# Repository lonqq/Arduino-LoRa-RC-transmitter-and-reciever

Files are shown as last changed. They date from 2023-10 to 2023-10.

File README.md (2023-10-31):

# Arduino based RC system
The ultimate DIY radio control system.
Remotely operate model airplanes, multicopters, boats, land vehicles, robots, or anything you can imagine.
<p align="left">
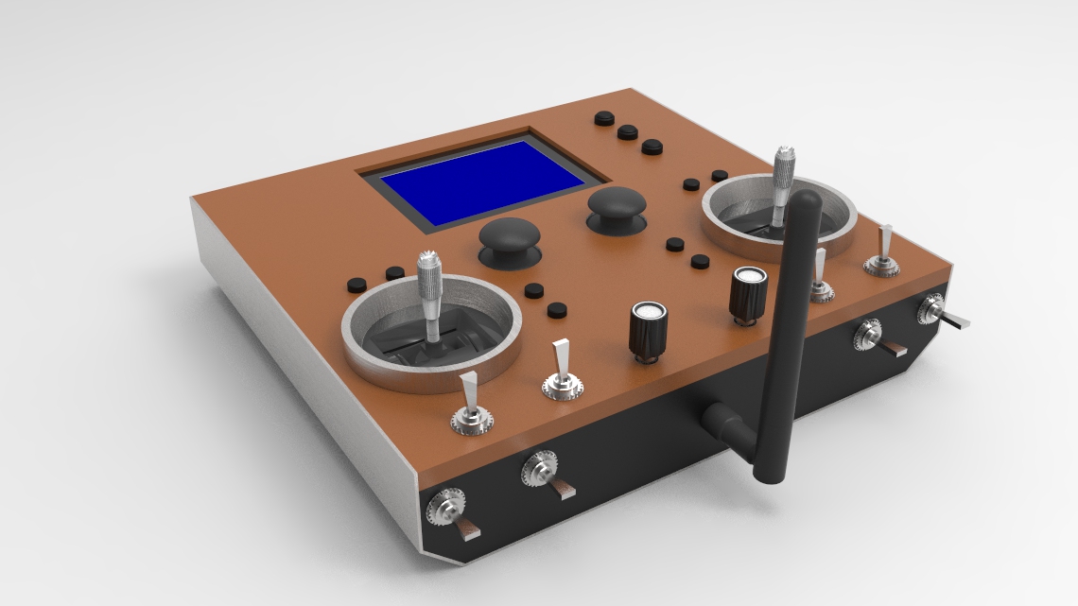
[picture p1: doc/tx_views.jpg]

</p>

## Main features
- 20 fully proportional RC channels, each channel encoded with 10 bits.
- Configurable RC channel output signal format.
- Update rate of 50x per second for all RC channels.
- Receiver binding, Adjustable RF power, Frequency hopping.
- Reverse, subtrim, endpoints, failsafe.
- Dual rates and expo, Custom curves, Flight modes.
- Powerful mixer system, Logical switches, Custom telemetry.
- Alarms, Warnings, Timers, etc.
- Intuitive user interface.
- Model memory. I2C eeprom and SD card supported.
- Model types, context-aware nomenclature; no need for land vehicles to have controls named after aircraft parts. 

## Hardware and Schematics
The schematics and related information can be found in the 'schematics' folder. 
The major components are as below.
- 1x Atmega2560 microcntroller, 2x Atmega328p microcontrollers.
- 2x SX1276/77/78/79 or RFM95 based Lora modules. However any module can possibly be used.
- 128x64 KS0108 based LCD. Any 128x64 LCD can however be used (provide own driver code).

## Compiling the firmware
The code compiles on arduino ide 1.8.x or later. The code is self-contained so doesn't require installing any libraries. 

## User Interface
Three buttons are used for navigation; Up, Select, Down. Long press Select to go Back.
<p align="left">

</p>

## Topics
[Mixer](doc/mixer.md)
<br>[Custom curves](doc/custom_curves.md)
<br>[Logical switches](doc/logical_switches.md)
<br>[Telemetry](doc/telemetry.md)
<br>[Receiver binding and configuration](doc/receiver_config.md)

## Frequently Asked Questions
[Got a question or an issue? See the FAQ first.](doc/faq.md)

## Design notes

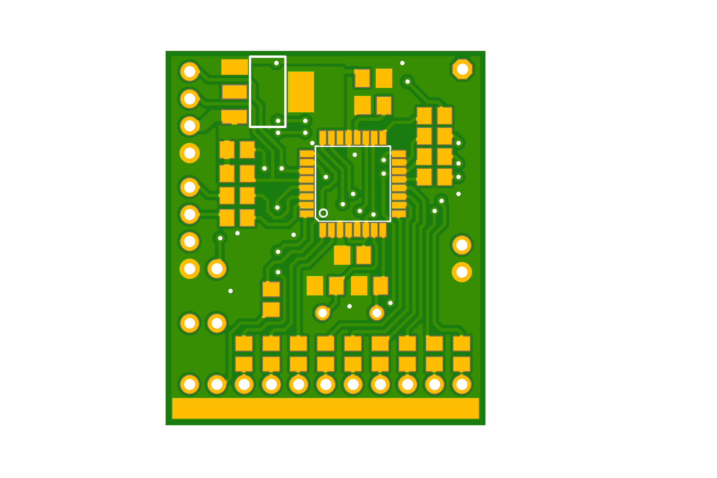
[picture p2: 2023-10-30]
schematics/receiver/rfm95/receiver_rfm95_5v.bottom.png

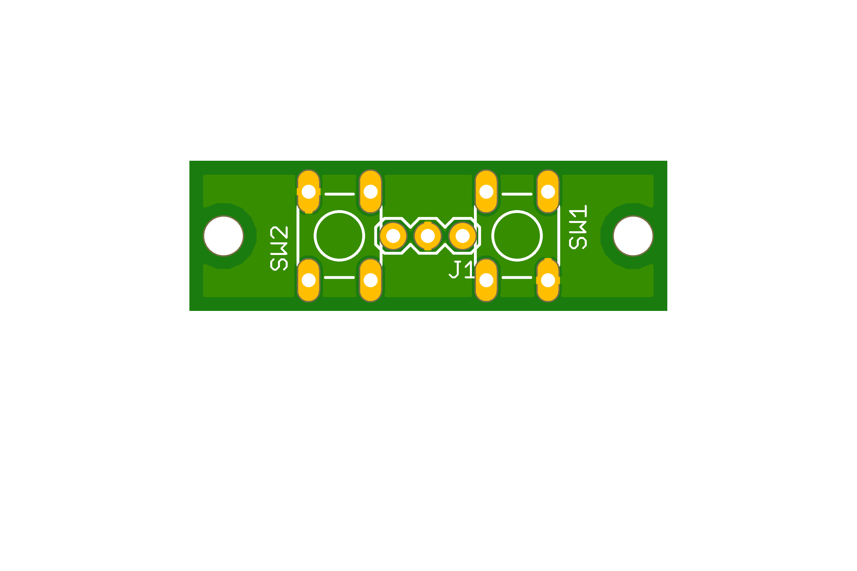
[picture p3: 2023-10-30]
schematics/transmitter/main/trims/trim_switch.top.png

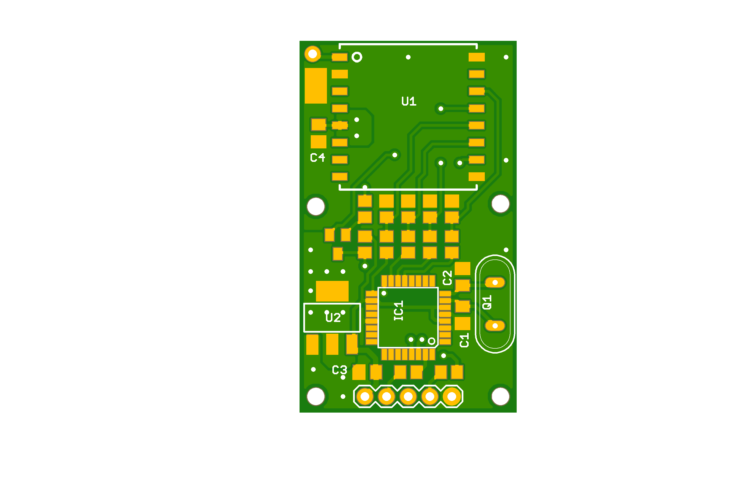
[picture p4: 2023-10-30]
schematics/transmitter/secondary/rfm95/junk/stx_rfm95.top.png

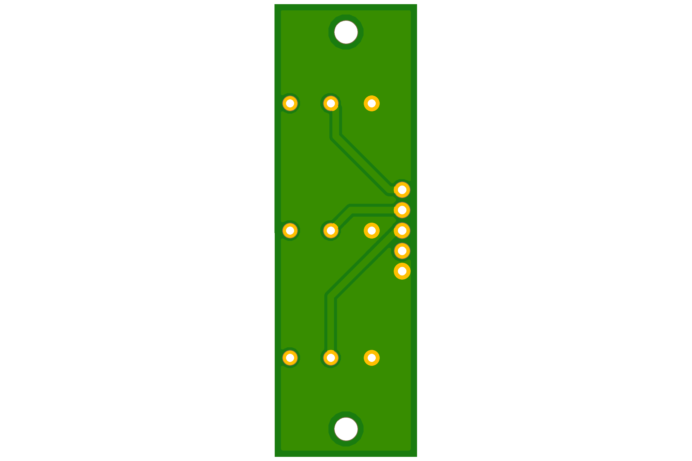
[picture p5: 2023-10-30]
schematics/transmitter/main/buttons/buttons.bottom.png

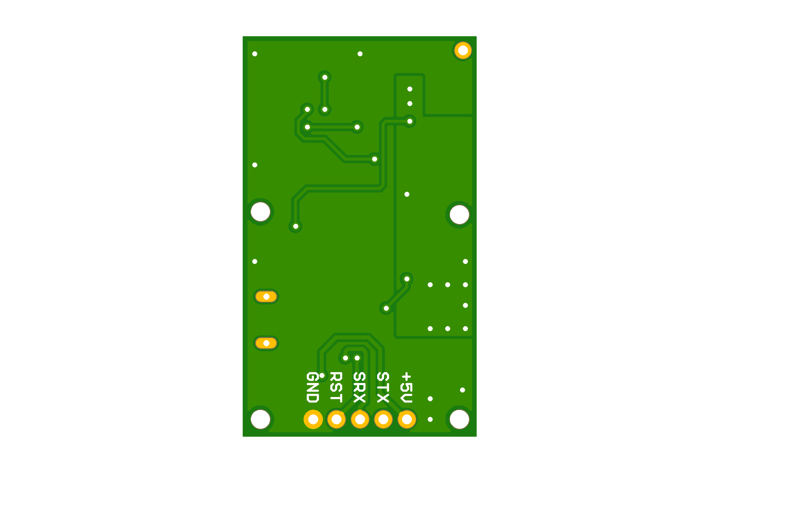
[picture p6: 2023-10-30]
schematics/transmitter/secondary/ra02/junk/stx_ra02.bottom.png

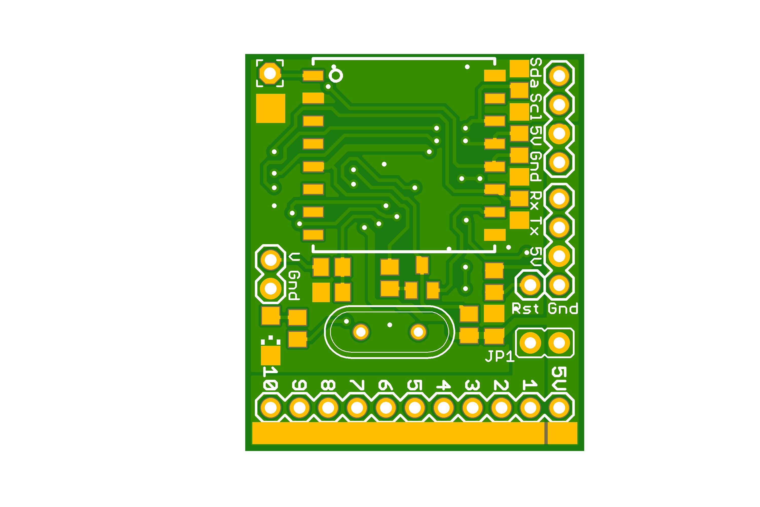
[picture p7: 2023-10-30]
schematics/receiver/rfm95/receiver_rfm95_5v.top.png

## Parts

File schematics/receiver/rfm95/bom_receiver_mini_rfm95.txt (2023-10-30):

Partlist exported from D:/Ba/rc radio project/New stuff/Beta14/schematics/receiver/rfm95/receiver_mini_rfm95.sch at 2023-05-28 19:32

Part Value             Device             Package   Description                
C1   22p               C-EUC0805K         C0805K    CAPACITOR, European symbol 
C2   22p               C-EUC0805K         C0805K    CAPACITOR, European symbol 
C3   100n              C-EUC0805K         C0805K    CAPACITOR, European symbol 
C4   100n              C-EUC0805K         C0805K    CAPACITOR, European symbol 
IC1  ATMEGA328P        MEGA8-AI           TQFP32-08 MICROCONTROLLER            
J1                     M05PTH             1X05      Header 5                   
PAD1                   2,15/1,0           2,15/1,0  THROUGH-HOLE PAD           
Q1   16MHz             XTAL/S             QS        CRYSTAL                    
Q2                     BC817-16SMD        SOT23-BEC NPN Transistor             
R1   10k               R-US_R0805         R0805     RESISTOR, American symbol  
R2   10k               R-US_R0805         R0805     RESISTOR, American symbol  
R3   10k               R-US_R0805         R0805     RESISTOR, American symbol  
R4   10k               R-US_R0805         R0805     RESISTOR, American symbol  
R5   10k               R-US_R0805         R0805     RESISTOR, American symbol  
R6   10k               R-US_R0805         R0805     RESISTOR, American symbol  
R7   5.6k              R-US_R0805         R0805     RESISTOR, American symbol  
R8   5.6k              R-US_R0805         R0805     RESISTOR, American symbol  
R9   5.6k              R-US_R0805         R0805     RESISTOR, American symbol  
R10  5.6k              R-US_R0805         R0805     RESISTOR, American symbol  
R11  5.6k              R-US_R0805         R0805     RESISTOR, American symbol  
R12  1k                R-US_R0805         R0805     RESISTOR, American symbol  
U1   RFM95_LORA_MODULE RFM95_LORA_MODULE  RFM95                                
U2   AMS1117_3.3       V_REG_LM1117SOT223 SOT223    Voltage Regulator LM1117

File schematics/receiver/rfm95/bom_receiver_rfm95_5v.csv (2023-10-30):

Part | Value | Device | Package | Description
C1 | 22p | C-EUC0805K | C0805K | CAPACITOR, European symbol
C2 | 22p | C-EUC0805K | C0805K | CAPACITOR, European symbol
C3 | 100n | C-EUC0805K | C0805K | CAPACITOR, European symbol
C4 | 100n | C-EUC0805K | C0805K | CAPACITOR, European symbol
C5 | 100n | C-EUC0805K | C0805K | CAPACITOR, European symbol
C6 | 100n | C-EUC0805K | C0805K | CAPACITOR, European symbol
IC1 | ATMEGA328P | MEGA8-AI | TQFP32-08 | MICROCONTROLLER
J1 |  | M02PTH | 1X02 | Standard 2-pin 0.1 header. Use with"
J2 |  | M04PTH | 1X04 | Header 4
J3 |  | M04PTH | 1X04 | Header 4
J4 |  | M01PTH | 1X01 | Header 1
J6 |  | M11PTH | 1X11 | Header 11
JP1 |  | JP1E | JP1 | JUMPER
LED1 |  | LEDCHIPLED_1206 | CHIPLED_1206 | LED
PAD1 |  | 2,15/1,0 | 2,15/1,0 | THROUGH-HOLE PAD
Q1 | 16MHz | XTAL/S | QS | CRYSTAL
Q2 |  | BC817-16SMD | SOT23-BEC | NPN Transistor
R1 | 10k | R-US_R0805 | R0805 | RESISTOR, American symbol
R2 | 10k | R-US_R0805 | R0805 | RESISTOR, American symbol
R3 | 1k | R-US_R0805 | R0805 | RESISTOR, American symbol
R4 | 10k | R-US_R0805 | R0805 | RESISTOR, American symbol
R5 | 10k | R-US_R0805 | R0805 | RESISTOR, American symbol
R6 | 10k | R-US_R0805 | R0805 | RESISTOR, American symbol
R7 | 5.6k | R-US_R0805 | R0805 | RESISTOR, American symbol
R8 | 10k | R-US_R0805 | R0805 | RESISTOR, American symbol
R9 | 5.6k | R-US_R0805 | R0805 | RESISTOR, American symbol
R10 | 5.6k | R-US_R0805 | R0805 | RESISTOR, American symbol
R11 | 5.6k | R-US_R0805 | R0805 | RESISTOR, American symbol
R12 | 5.6k | R-US_R0805 | R0805 | RESISTOR, American symbol
R13 | 15k | R-US_R0805 | R0805 | RESISTOR, American symbol
R15 | 1k | R-US_R0805 | R0805 | RESISTOR, American symbol
R16 | 5.6k | R-US_R0805 | R0805 | RESISTOR, American symbol
R17 | 5.6k | R-US_R0805 | R0805 | RESISTOR, American symbol
R18 | 1k | R-US_R0805 | R0805 | RESISTOR, American symbol
R19 | 1k | R-US_R0805 | R0805 | RESISTOR, American symbol
R20 | 1k | R-US_R0805 | R0805 | RESISTOR, American symbol
R21 | 1k | R-US_R0805 | R0805 | RESISTOR, American symbol
R22 | 1k | R-US_R0805 | R0805 | RESISTOR, American symbol
R23 | 1k | R-US_R0805 | R0805 | RESISTOR, American symbol
R24 | 1k | R-US_R0805 | R0805 | RESISTOR, American symbol
R25 | 1k | R-US_R0805 | R0805 | RESISTOR, American symbol
R26 | 1k | R-US_R0805 | R0805 | RESISTOR, American symbol
R27 | 1k | R-US_R0805 | R0805 | RESISTOR, American symbol
R28 | 1k | R-US_R0805 | R0805 | RESISTOR, American symbol
R29 | 1k | R-US_R0805 | R0805 | RESISTOR, American symbol
U1 | RFM95_LORA_MODULE | RFM95_LORA_MODULE | RFM95
U2 | AMS1117_3.3 | V_REG_LM1117SOT223 | SOT223 | Voltage Regulator LM1117

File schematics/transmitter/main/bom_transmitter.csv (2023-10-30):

Part | Value | Device | Package | Description
C1 | 22pF | C-EU050-024X044 | C050-024X044 | CAPACITOR, European symbol
C2 | 22pF | C-EU050-024X044 | C050-024X044 | CAPACITOR, European symbol
C3 | 100nF | C-EU050-024X044 | C050-024X044 | CAPACITOR, European symbol
C4 | 100n | C-EU050-024X044 | C050-024X044 | CAPACITOR, European symbol
C5 | 100uF | CPOL-USE2,5-6E | E2,5-6E | POLARIZED CAPACITOR, American symbol
C6 | 100n | C-EU050-024X044 | C050-024X044 | CAPACITOR, European symbol
C8 | 100nF | C-EU050-024X044 | C050-024X044 | CAPACITOR, European symbol
C9 | 100nF | C-EU050-024X044 | C050-024X044 | CAPACITOR, European symbol
C10 | 100nF | C-EU050-024X044 | C050-024X044 | CAPACITOR, European symbol
C11 | 100nF | C-EU050-024X044 | C050-024X044 | CAPACITOR, European symbol
C12 | 1uF | C-EU050-024X044 | C050-024X044 | CAPACITOR, European symbol
C13 | 100nF | C-EU050-024X044 | C050-024X044 | CAPACITOR, European symbol
C14 | 100nF | C-EU050-024X044 | C050-024X044 | CAPACITOR, European symbol
C15 | 100nF | C-EU050-024X044 | C050-024X044 | CAPACITOR, European symbol
C16 | 100nF | C-EU050-024X044 | C050-024X044 | CAPACITOR, European symbol
C17 | 100nF | C-EU050-024X044 | C050-024X044 | CAPACITOR, European symbol
C18 | 100nF | C-EU050-024X044 | C050-024X044 | CAPACITOR, European symbol
C19 | 100n | C-EU050-024X044 | C050-024X044 | CAPACITOR, European symbol
C20 | 100nF | C-EU050-024X044 | C050-024X044 | CAPACITOR, European symbol
C21 | 100nF | C-EU050-024X044 | C050-024X044 | CAPACITOR, European symbol
C22 | 100nF | C-EU050-024X044 | C050-024X044 | CAPACITOR, European symbol
C23 | 100nF | C-EU050-024X044 | C050-024X044 | CAPACITOR, European symbol
D1 | 1N5819 | 1N5817-B | DO41-7.6 | 1.0A SCHOTTKY BARRIER RECTIFIER
D2 | 1N5819 | 1N5817-B | DO41-7.6 | 1.0A SCHOTTKY BARRIER RECTIFIER
D3 | 1N5819 | 1N5817-B | DO41-7.6 | 1.0A SCHOTTKY BARRIER RECTIFIER
J1 |  | M01PTH_LONGPAD | 1X01_LONGPAD | Header 1
J2 |  | M01PTH_LONGPAD | 1X01_LONGPAD | Header 1
OK1 | PC817 | PC817 | DIL04 | SHARP OPTO COUPLER
Q1 | 16MHz | XTAL/S | QS | CRYSTAL
Q2 | P_MOSFET | FDN360P | SUPER-SOT3 | Single P-Channel, PowerTrench (R) MOSFET
R1 | 1k | R-US_0204/5 | 0204/5 | RESISTOR, American symbol
R2 | 1k | R-US_0204/5 | 0204/5 | RESISTOR, American symbol
R3 | 1k | R-US_0204/5 | 0204/5 | RESISTOR, American symbol
R4 | 10k | R-US_0204/5 | 0204/5 | RESISTOR, American symbol
R5 | 220k | R-US_0204/5 | 0204/5 | RESISTOR, American symbol
R6 | 10k | R-US_0204/5 | 0204/5 | RESISTOR, American symbol
R7 | 220k | R-US_0204/5 | 0204/5 | RESISTOR, American symbol
R8 | 10k | R-US_0204/5 | 0204/5 | RESISTOR, American symbol
R9 | 4.7k | R-US_0204/5 | 0204/5 | RESISTOR, American symbol
R10 | 4.7k | R-US_0204/5 | 0204/5 | RESISTOR, American symbol
R11 | 1k | TRIMPOTPTH | TRIM_POT_PTH | Various small potentiometers for set-and-forget" applications"
R12 | 10k | R-US_0204/5 | 0204/5 | RESISTOR, American symbol
R13 | 1k | R-US_0204/5 | 0204/5 | RESISTOR, American symbol
R14 | 3.3k | R-US_0204/5 | 0204/5 | RESISTOR, American symbol
R15 | 47 | R-US_0204/5 | 0204/5 | RESISTOR, American symbol
R16 | 3.3k | R-US_0204/5 | 0204/5 | RESISTOR, American symbol
R17 | 1k | R-US_0204/5 | 0204/5 | RESISTOR, American symbol
R18 | 47 | R-US_0204/5 | 0204/5 | RESISTOR, American symbol
R19 | 1k | R-US_0204/5 | 0204/5 | RESISTOR, American symbol
R20 | 1k | R-US_0204/5 | 0204/5 | RESISTOR, American symbol
R21 | 1k | R-US_0204/5 | 0204/5 | RESISTOR, American symbol
R22 | 680 | R-US_0204/5 | 0204/5 | RESISTOR, American symbol
R23 | 680 | R-US_0204/5 | 0204/5 | RESISTOR, American symbol
R24 | 680 | R-US_0204/5 | 0204/5 | RESISTOR, American symbol
R25 | 1k | R-US_0204/5 | 0204/5 | RESISTOR, American symbol
R26 | 1k | R-US_0204/5 | 0204/5 | RESISTOR, American symbol
R27 | 1k | R-US_0204/5 | 0204/5 | RESISTOR, American symbol
R28 | 2.2k | R-US_0204/5 | 0204/5 | RESISTOR, American symbol
R29 | 2.2k | R-US_0204/5 | 0204/5 | RESISTOR, American symbol
SV1 |  | MA05-1 | MA05-1 | PIN HEADER
SV2 |  | MA03-1 | MA03-1 | PIN HEADER
SV3 |  | MA03-1 | MA03-1 | PIN HEADER
SV4 |  | MA03-1 | MA03-1 | PIN HEADER
SV5 |  | MA03-1 | MA03-1 | PIN HEADER
SV6 |  | MA03-1 | MA03-1 | PIN HEADER
SV7 |  | MA03-1 | MA03-1 | PIN HEADER
SV8 |  | MA03-1 | MA03-1 | PIN HEADER
SV9 |  | MA03-1 | MA03-1 | PIN HEADER
SV10 |  | MA03-1 | MA03-1 | PIN HEADER
SV11 |  | MA03-1 | MA03-1 | PIN HEADER
SV12 |  | MA03-1 | MA03-1 | PIN HEADER
SV13 |  | MA03-1 | MA03-1 | PIN HEADER
SV14 |  | MA05-1 | MA05-1 | PIN HEADER
SV15 | ICSP | MA03-2 | MA03-2 | PIN HEADER
SV16 |  | MA03-1 | MA03-1 | PIN HEADER
SV17 |  | MA03-1 | MA03-1 | PIN HEADER
SV18 |  | MA03-1 | MA03-1 | PIN HEADER
SV19 |  | MA03-1 | MA03-1 | PIN HEADER
SV20 |  | MA03-1 | MA03-1 | PIN HEADER
SV21 |  | MA03-1 | MA03-1 | PIN HEADER
SV22 |  | MA03-1 | MA03-1 | PIN HEADER
SV23 |  | MA03-1 | MA03-1 | PIN HEADER
SV24 |  | MA03-1 | MA03-1 | PIN HEADER
SV25 |  | MA03-1 | MA03-1 | PIN HEADER
SV26 |  | MA20-1 | MA20-1 | PIN HEADER
SV27 |  | MA05-1 | MA05-1 | PIN HEADER
SV28 |  | MA05-1 | MA05-1 | PIN HEADER
SV29 |  | MA05-1 | MA05-1 | PIN HEADER
SV30 |  | MA03-1 | MA03-1 | PIN HEADER
SV31 |  | MA03-1 | MA03-1 | PIN HEADER
SV32 |  | MA03-1 | MA03-1 | PIN HEADER
SV33 |  | MA03-1 | MA03-1 | PIN HEADER
SV34 |  | MA03-1 | MA03-1 | PIN HEADER
T1 | BC337 | BC337 | TO92 | NPN TRANSISTOR
T2 | BC337 | BC337 | TO92 | NPN TRANSISTOR
T3 | BC337 | BC337 | TO92 | NPN TRANSISTOR
T4 | BC337 | BC337 | TO92 | NPN TRANSISTOR
U$1 | MICROSD-PUSH-OUT | MICROSD-PUSH-OUT | MICROSD-PUSH-OUT | T-Flash Push-Out Micro SD Card Reader
U1 | EEPROM-I2C | EEPROM-I2CEIAJ | SO08-EIAJ | I2C EEPROM chips, 24LC256 (and others)
U2 | AMS1117_5V | V_REG_LM1117SOT223 | SOT223 | Voltage Regulator LM1117
U3 | AMS1117_5V | V_REG_LM1117SOT223 | SOT223 | Voltage Regulator LM1117
U4 | ATMEGA2560AU | ATMEGA2560AU | TQFP100 | Atmel 100-pin 8-bit uC
U5 | AMS1117_3V3 | V_REG_LM1117SOT223 | SOT223 | Voltage Regulator LM1117

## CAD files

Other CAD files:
Drawings/plan_top_plate.SLDDRW
Drawings/plan_top_plate.skp
Drawings/radio_mockup.skp

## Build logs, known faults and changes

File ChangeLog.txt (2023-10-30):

3.0
--------
Hardware changes:
 - Moved to Atmega2560 microcontroller. The Atmega328 was quite limiting thus 2.2 is the last branch to support it.
 - Redesigned both transmitter and receiver hardware

Firmware changes:
 - Redesigned the mixer. This new mixer borrows some ideas from OpenTx(R).
 - Added flight modes, custom curves, logical switches, counters.
 - Redesigned timers, function generators.
 - Added custom telemetry.
 - Improved safety Warnings for throttle and switch positions.
 - Support for external EEPROM to store model data.
 - Support for SD card model backups.
 - Home screen widgets to display various information.
 - Various optimizations and improvements.
 - Major code refactoring.
 - Redesigned the serial data and air protocols.
 - etc.

2.2
--------
06Mar2022
 - Fixed minor glitch in function generator.
 
16Feb2022
 - Added a simple function generator. Useful for testing stuff like servos. 
   It can be configured to output periodic motion like sine, square, triangle, and sawtooth.

2.1
--------
02Jan2022
 - Support for KS0108 lcds with active low chip select pins. Enable by uncommenting CS_ACTIVE_LOW in the LCDKS0108.h file

17Aug2021
 - Fixed undesirable behaviour of differential in mixer when trim is non-zero
 - Order of operation in mixer is changed. Now as weight->offset->differential->trim(weighted)

July2021
 - Added two more switches SwE and SwF.
 - Added soft power latching control.
 - Improved sounds handling. Added sounds for trim mode entry and exit.
 - Show voltage telemetry on home screen.
 - Reduced occasional clashing of audio. 
 - 9 channels, all can be configured from the transmitter to output servo pwm, normal pwm, or digital (on-off) signals.
 - Redesigned the serial communication format and the air protocol.
 - Telemetry thresholds are stored on model basis.
 - Optimised GFX library.
 - UI improvements.
 - Code refactoring.

1.7.0
-----
21Mar2021
 - Bound receiver is remembered if bind is initiated but fails, for instance if we uintentionally enter bind in transmitter.
 
Feb2021
 - Added External voltage telemetry. Useful for knowing model battery voltage so know when to land, instead of 
   relying on a timer.
 - Slight modification to receiver schematic to enable measuring external voltage.
 - Improved receiver binding.
 - Improved model management.
 - Other subtle code optimisations

1.6.0
-----
31Jan2021
 - Added confirmation screens to ui for model copy, model reset, mixer reset
 - Can now use lower case letters in model name.
 - Other minor improvements.
 - Timer 1 is now adaptable. We can specify a control source.
 - Inherent throttle cut feature dropped. Throttle cut should instead be programmed in the mixer.

21Jan2021
 - Reduced receiver startup time. 
 - Minor improvements to 'Model' screen.
 - Other minor improvemnts.
 
06Jan2021
 - Flash LED on successful bind

21Dec2020
 - User selectable transmitter rf power.
 - Easily discernible audio beeps for trim to help tell which input we are trimming.
 
16Nov2020
 - Added 'Slow' function for switches, usable on only one switch. The source switch has its name
   displayed with an asterisk in mixer.
 - Removed hard-coded slowing of all switches in mixer. This could only be overcome with workarounds.
 - Redesigned some layouts in gui.
 - Removed mixer templates for crow braking and flaperon.
 - Using single variable for all channel reverse. An array was quite wasteful for boolean data.
 - Removed automatic formating of eeprom when default system or model values are edited.
 - Other minor code improvements.

1.5.0
-----
01Nov2020
 - Autodetect if eeprom needs formating
 
31Oct2020
 - Moved transmitterID generation and storage to secondary mcu
 
26Oct2020
 - Code refactor: using signed types where necessary
 - Minor improvements in stick calibration screen
 - Subtle tweaks to menu
 
24Oct2020
 - Added control switch in mixer. This can be used to easily turn on of off the mix.
 - Added Replace option in mixer multiplex. This works best when combined with a switch.
 - Various code improvements
 
20Oct2020
 - Added a custom 5 point curve
 - Renamed menu entry 'Curves' to 'Inputs'
 - Added preview of all raw input sources in Inputs screen
 
18Oct2020
 - Added mixer templates for elevon, vtail, flaperon, crow braking, and differential thrust
 
10Oct2020
 - Updated frequency list
 - Added bind flag in transmitted packets
 
06Oct2020
 - Implemented binding and frequency hopping

1.4.0
-----
 04Oct2020
  - Fixed minor bug introduced in cut switch behaviour. 

 26Sep2020
  - Corrected minor flaw in pre mixer where adding trim resulted in out of range values

 25Sep2020
  - Model data now saved when trim has been adjusted. This was a forgotten feature. 
  - SwA can now be used in the mixer.
  - Throttle warning can now only be passed when the throttle stick is moved to minimum.

 23Sep2020
  - Using structs now to ease model data and system data management with eeprom. The structures are 
    now copied effortlessly between ram and eeprom. This also saved us lots of flash. 
  - Added hidden boot menu. 
  - Added trims for Ail, Ele, Thr, Rud, accesible on the home screen.
  - Removed battery calibration, it was unnecessary in code and rarely used. It is a set once thing. 
  - Removed popup menu in system settings screen.
  - Stick calibration moved to hidden boot screen. 
  - Code clean up.

1.3.0
-----
 06Sep2020
  - Removed the reading and averaging several stick samples in code. This was rather unneccesary as 
    there are already capacitors for smoothing. This saved about 2ms of main loop.
 
 01Sep2020
  - Removed hardcoded timings dependent on loop counter.
 
 30Aug2020
  - Minor fixes in secondary mcu code
 
 29Aug2020
  - cleaned up receiver mcu code
 
 23Aug2020
  - Minor code improvements and cleanup
 
 18Aug2020
  - Removed unused stuff like text size and text background color from GFX lib to speed up character
    draw operations.
  - Speeded up SPI clock in LCD driver library.
 
 16Aug2020
  - Improved button events in UI. Now have pressed, clicked, held button events.
  - Fixed button handling in extended channels mode
 
 15Aug2020
  - Minor UI changes; context menu trigger moved to icon in top right of screen. Long pressing down 
    or up fast scrolls through the entries / fields.
 
 04Aug2020
  - Minor UI improvements. 
 
 02Aug2020
  - Replaced triangle waveform with stepped sine waveform
 
 28July2020
  - Slimmed down GFX library to save flash space and some ram. Unused stuff like Bresenham's line 
    algorithm, etc have been removed, and some functions have been rewritten for speed.
  - Skipped checking screen rotation (unused) in lcd driver library to speed up draw operations.
 
 18July2020
  - Backlight time now configurable
 
 12July2020
  - Slight improvements in battery warning handling, now self dismissing after 3 seconds. 
  - Slight improvements in battery gauge
 
 08July2020
  - added battery factor, battery min and battery max to advanced setup screen. Also moved stick 
    calibration to this screen
 
 26June2020 
  - Can configure pwm mode for ch3 (throttle) to either servo pulse or ordinary pwm. This is useful 
    for controlling brushed dc motors directly by the receiver without signal conversion circuits.
  - Improved master to slave serial communication. 
  - Code cleanup

1.2.0
------
 10June2020
  - Replaced all floating point maths with equivalent integer implementation

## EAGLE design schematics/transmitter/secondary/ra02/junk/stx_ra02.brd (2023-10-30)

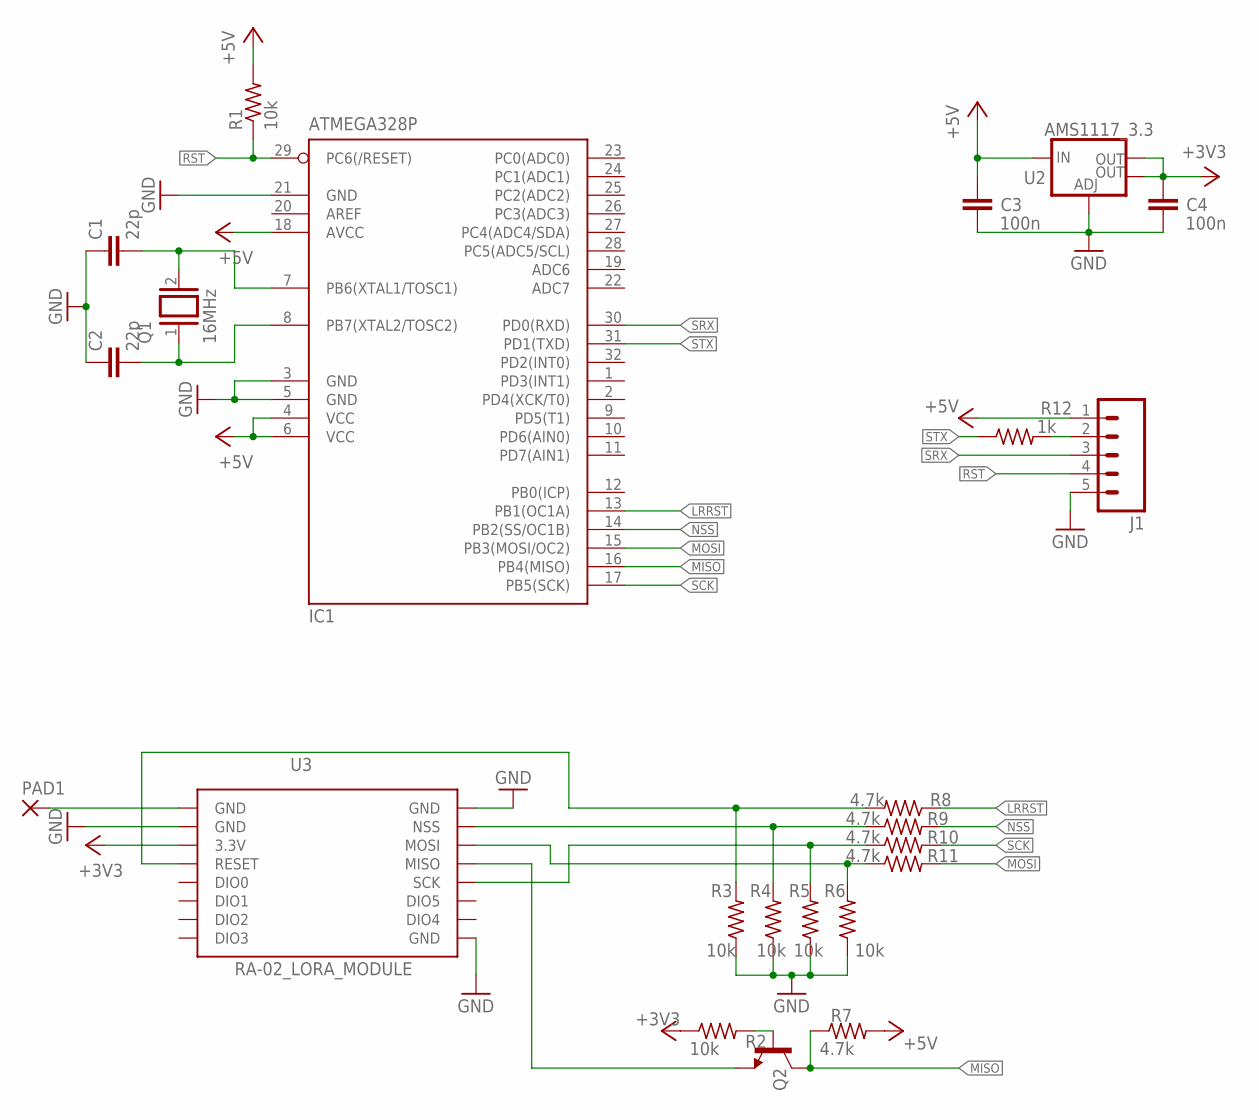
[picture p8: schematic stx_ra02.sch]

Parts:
C1, C2: 22p; C0805K
C3, C4: 100n; C0805K
IC1: ATMEGA328P; TQFP32-08
J1: M05PTH; 1X05
PAD1: 2,15/1,0
Q1: 16MHz; QS
Q2: BC817-16SMD; SOT23-BEC
R1, R2, R3, R4, R5, R6: 10k; R0805
R7, R8, R9, R10, R11: 4.7k; R0805
R12: 1k; R0805
U2: AMS1117_3.3; SOT223
U3: RA-02_LORA_MODULE; RA-02

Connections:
+3V3: C4.2, R2.1, U2.2 (OUT), U2.4 (OUT), U3.3.3V
+5V: C3.2, IC1.4 (VCC), IC1.6 (VCC), IC1.18 (AVCC), J1.1, R1.2, R7.2, U2.3 (IN)
GND: C1.1, C2.1, C3.1, C4.1, IC1.3 (GND), IC1.5 (GND), IC1.21 (GND), J1.5, R3.1, R4.1, R5.1, R6.1, U2.1 (ADJ), U3.GND@2 (GND), U3.GND@3 (GND), U3.GND@4 (GND)
LRRST: IC1.13 (PB1(OC1A)), R8.1
MISO: IC1.16 (PB4(MISO)), Q2.C, R7.1
MOSI: IC1.15 (PB3(MOSI/OC2)), R11.2
unnamed: C1.2, IC1.7 (PB6(XTAL1/TOSC1)), Q1.2
unnamed: J1.2, R12.2
unnamed: C2.2, IC1.8 (PB7(XTAL2/TOSC2)), Q1.1
unnamed: R3.2, R8.2, U3.RESET
unnamed: PAD1.1, U3.GND
unnamed: Q2.E, U3.MISO
unnamed: R4.2, R9.1, U3.NSS
unnamed: R5.2, R10.1, U3.SCK
unnamed: R6.2, R11.1, U3.MOSI
unnamed: Q2.B, R2.2
NSS: IC1.14 (PB2(SS/OC1B)), R9.2
RST: IC1.29 (PC6(/RESET)), J1.4, R1.1
SCK: IC1.17 (PB5(SCK)), R10.2
SRX: IC1.30 (PD0(RXD)), J1.3
STX: IC1.31 (PD1(TXD)), R12.1

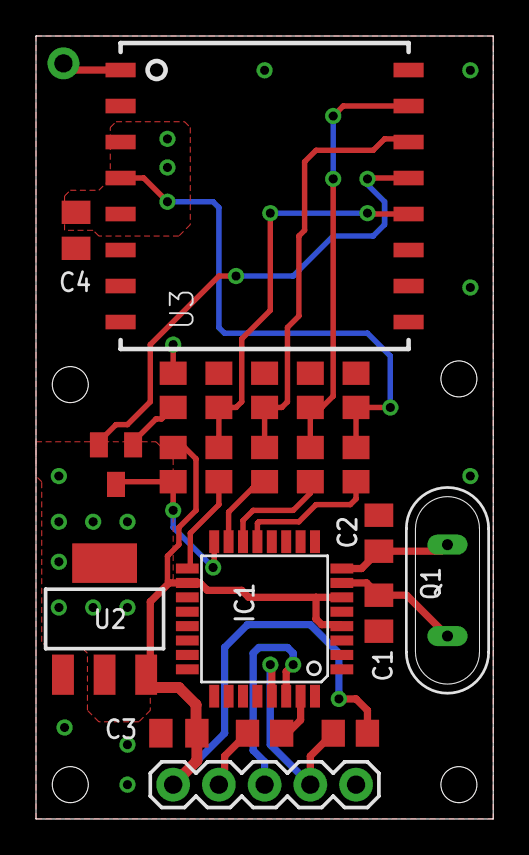
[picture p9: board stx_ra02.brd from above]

Board: 2 copper layers, 25.4 x 43.5 mm, 23 parts (0 on the bottom side), 21 nets.

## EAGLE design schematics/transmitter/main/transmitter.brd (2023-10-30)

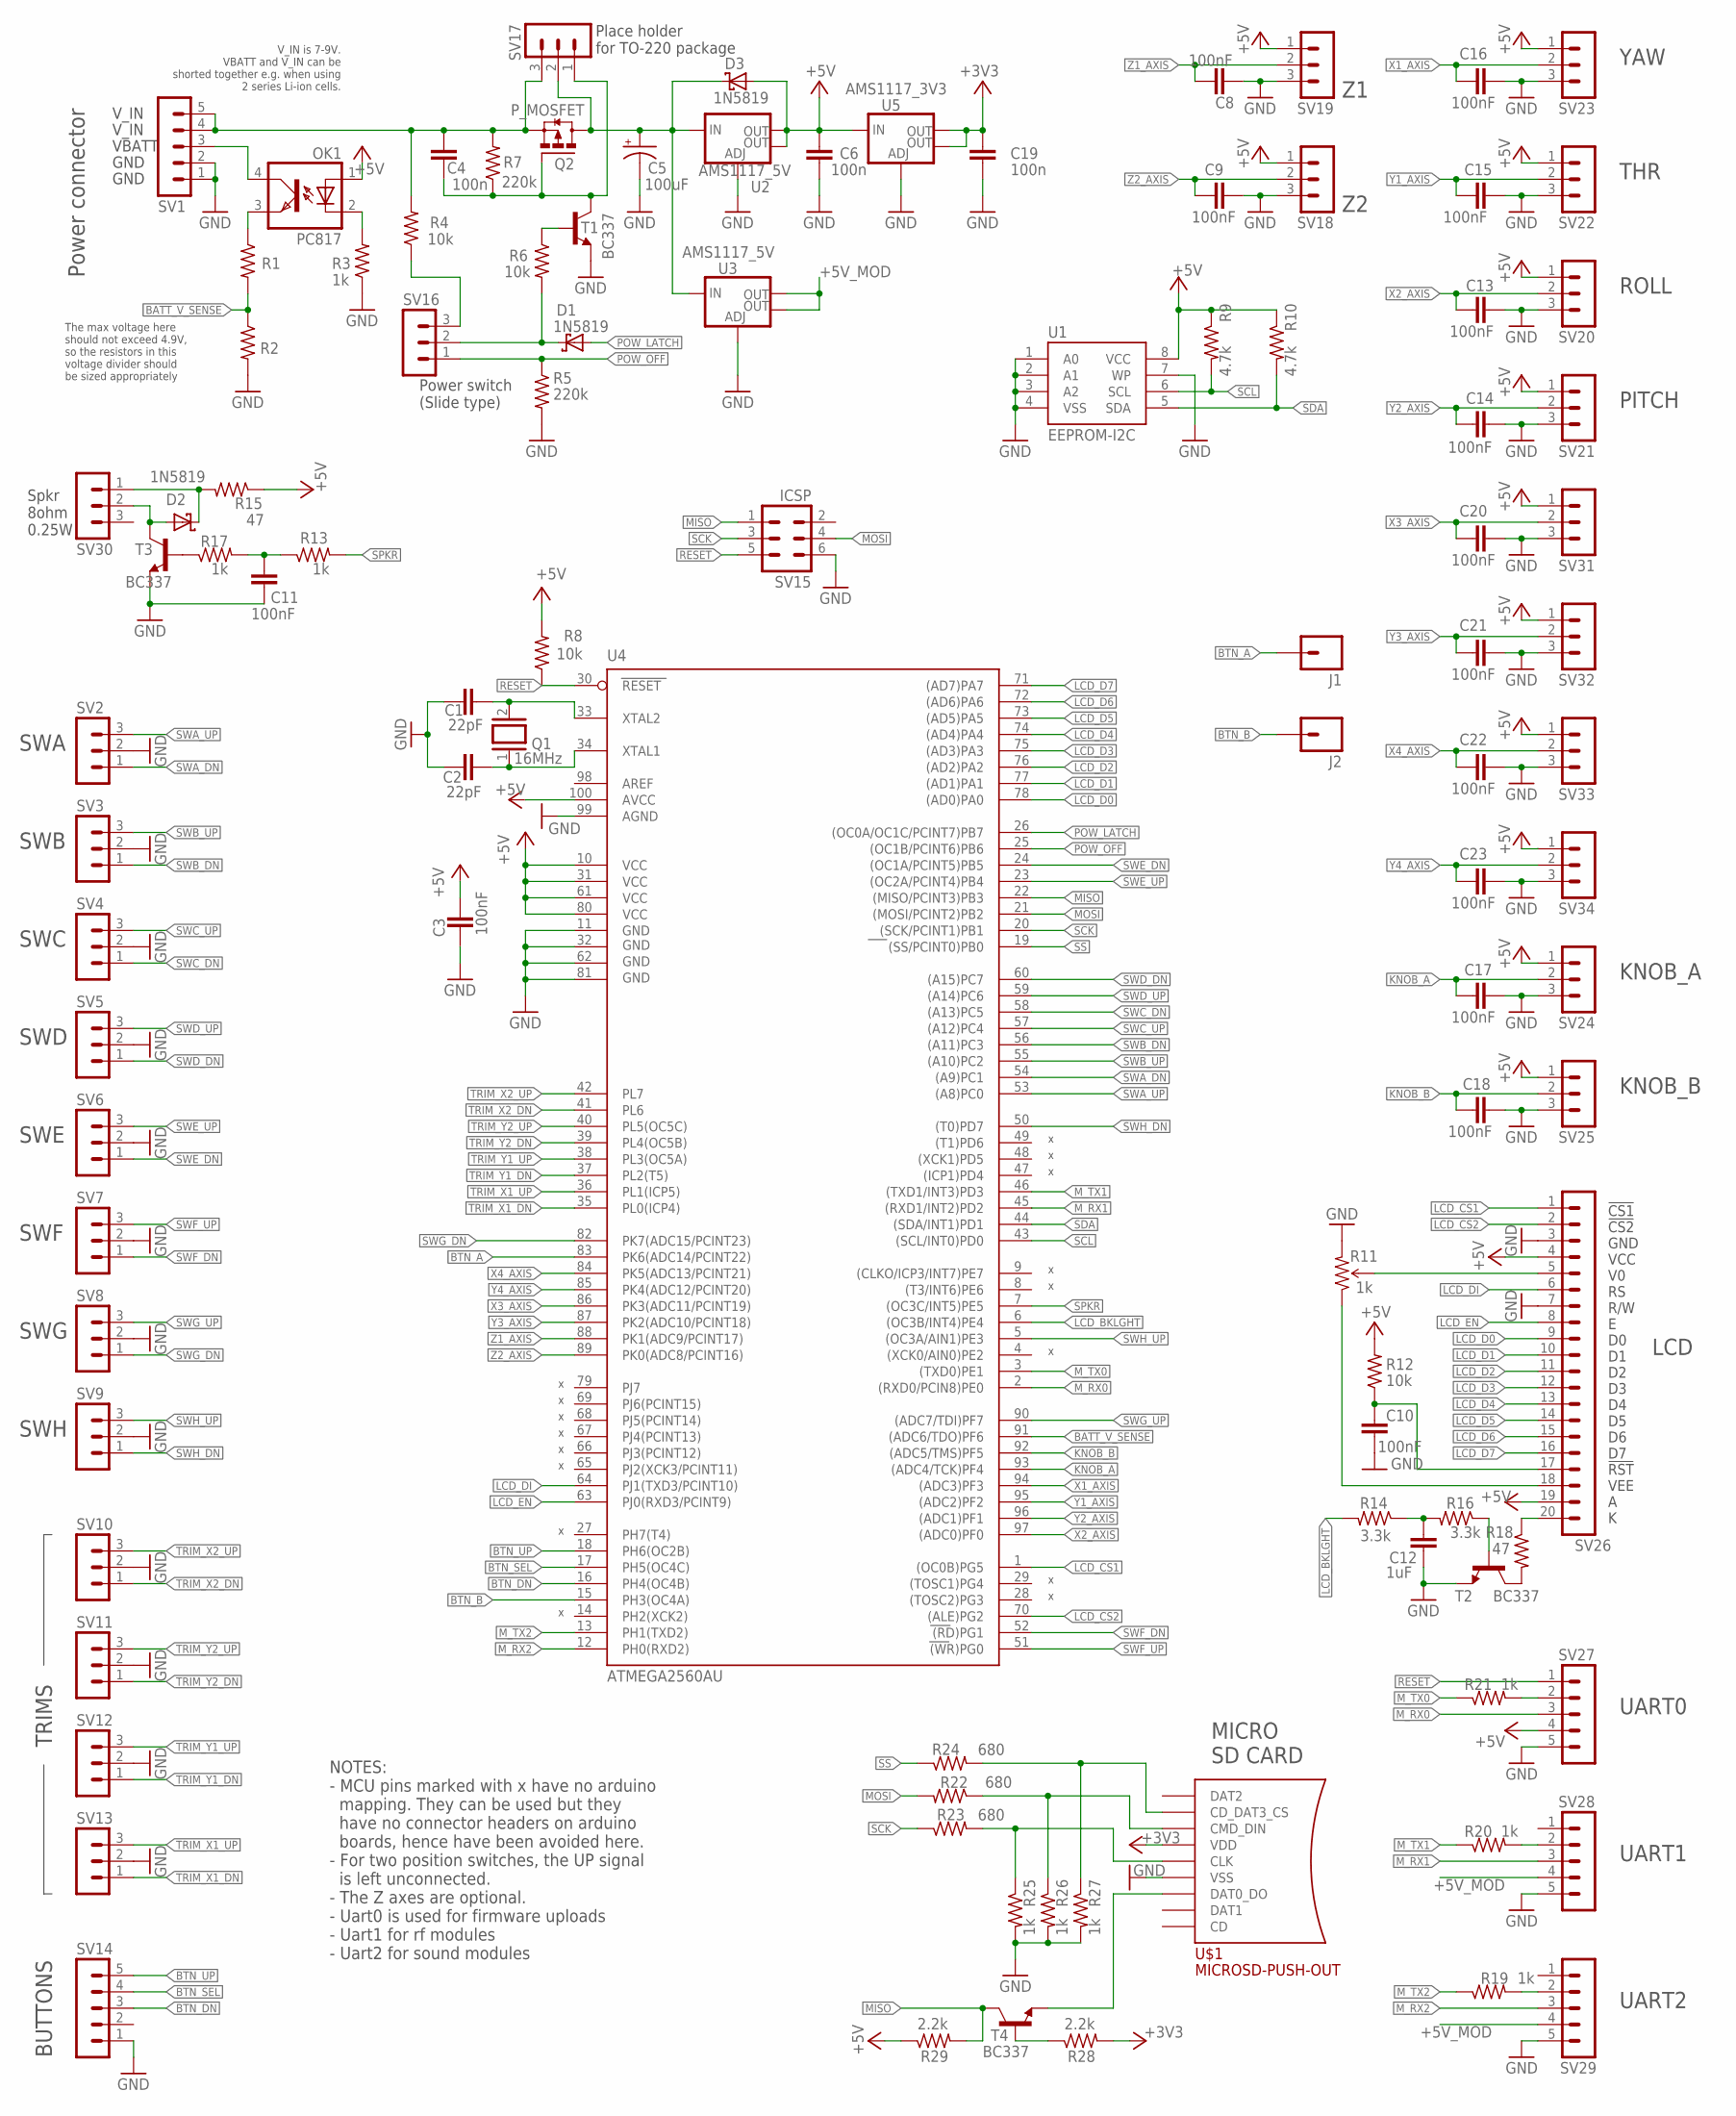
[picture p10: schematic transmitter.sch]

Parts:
C1, C2: 22pF; C050-024X044
C3, C8, C9, C10, C11, C13, C14, C15, C16, C17, C18, C20, C21, C22, C23: 100nF; C050-024X044
C4, C6, C19: 100n; C050-024X044
C5: 100uF; E2,5-6E
C12: 1uF; C050-024X044
D1, D2, D3: 1N5819; DO41-7.6
J1, J2: M01PTH_LONGPAD; 1X01_LONGPAD
OK1: PC817; DIL04
Q1: 16MHz; QS
Q2: P_MOSFET; SUPER-SOT3
R1, R2, R3, R13, R17, R19, R20, R21, R25, R26, R27: 1k; 0204/5
R4, R6, R8, R12: 10k; 0204/5
R5, R7: 220k; 0204/5
R9, R10: 4.7k; 0204/5
R11: 1k; TRIM_POT_PTH
R14, R16: 3.3k; 0204/5
R15, R18: 47; 0204/5
R22, R23, R24: 680; 0204/5
R28, R29: 2.2k; 0204/5
SV1, SV14, SV27, SV28, SV29: MA05-1
SV2, SV3, SV4, SV5, SV6, SV7, SV8, SV9, SV10, SV11, SV12, SV13, SV16, SV17, SV18, SV19, SV20, SV21, SV22, SV23, SV24, SV25, SV30, SV31, SV32, SV33, SV34: MA03-1
SV15: ICSP; MA03-2
SV26: MA20-1
T1, T2, T3, T4: BC337; TO92
U1: EEPROM-I2C; SO08-EIAJ
U2, U3: AMS1117_5V; SOT223
U4: ATMEGA2560AU; TQFP100
U5: AMS1117_3V3; SOT223
U$1: MICROSD-PUSH-OUT

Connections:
+3V3: C19.2, R28.2, U5.2 (OUT), U5.4 (OUT), U$1.4 (VDD)
+5V: C3.1, C6.2, D3.A, OK1.1 (A), R8.2, R9.1, R10.1, R12.2, R15.1, R29.1, SV18.1, SV19.1, SV20.1, SV21.1, SV22.1, SV23.1, SV24.1, SV25.1, SV26.4, SV26.19, SV27.4, SV31.1, SV32.1, SV33.1, SV34.1, U1.8 (VCC), U2.2 (OUT), U2.4 (OUT), U4.10 (VCC), U4.31 (VCC1), U4.61 (VCC2), U4.80 (VCC3), U4.100 (AVCC), U5.3 (IN)
+5V_MOD: SV28.4, SV29.4, U3.2 (OUT), U3.4 (OUT)
BATT_V_SENSE: R1.2, R2.1, U4.91 ((ADC6/TDO)PF6)
BTN_A: J1.1, U4.83 (PK6(ADC14/PCINT22))
BTN_B: J2.1, U4.15 (PH3(OC4A))
BTN_DN: SV14.3, U4.16 (PH4(OC4B))
BTN_SEL: SV14.4, U4.17 (PH5(OC4C))
BTN_UP: SV14.5, U4.18 (PH6(OC2B))
GND: C1.1, C2.1, C3.2, C5.-, C6.1, C8.2, C9.1, C10.2, C11.2, C12.2, C13.1, C14.1, C15.1, C16.1, C17.1, C18.1, C19.1, C20.1, C21.1, C22.1, C23.1, R2.2, R3.1, R5.2, R11.3 (CW), R25.2, R26.2, R27.2, SV1.1, SV1.2, SV2.2, SV3.2, SV4.2, SV5.2, SV6.2, SV7.2, SV8.2, SV9.2, SV10.2, SV11.2, SV12.2, SV13.2, SV14.1, SV15.6, SV18.3, SV19.3, SV20.3, SV21.3, SV22.3, SV23.3, SV24.3, SV25.3, SV26.3, SV26.7, SV27.5, SV28.5, SV29.5, SV31.3, SV32.3, SV33.3, SV34.3, T1.1 (E), T2.1 (E), T3.1 (E), U1.1 (A0), U1.2 (A1), U1.3 (A2), U1.4 (VSS), U1.7 (WP), U2.1 (ADJ), U3.1 (ADJ), U4.11 (GND), U4.32 (GND1), U4.62 (GND2), U4.81 (GND3), U4.99 (AGND), U5.1 (ADJ), U$1.6 (VSS), U$1.G1 (VSS), U$1.G2 (VSS), U$1.G3 (VSS), U$1.G4 (VSS)
KNOB_A: C17.2, SV24.2, U4.93 ((ADC4/TCK)PF4)
KNOB_B: C18.2, SV25.2, U4.92 ((ADC5/TMS)PF5)
LCD_BKLGHT: R14.2, U4.6 ((OC3B/INT4)PE4)
LCD_CS1: SV26.1, U4.1 ((OC0B)PG5)
LCD_CS2: SV26.2, U4.70 ((ALE)PG2)
LCD_D0: SV26.9, U4.78 ((AD0)PA0)
LCD_D1: SV26.10, U4.77 ((AD1)PA1)
LCD_D2: SV26.11, U4.76 ((AD2)PA2)
LCD_D3: SV26.12, U4.75 ((AD3)PA3)
LCD_D4: SV26.13, U4.74 ((AD4)PA4)
LCD_D5: SV26.14, U4.73 ((AD5)PA5)
LCD_D6: SV26.15, U4.72 ((AD6)PA6)
LCD_D7: SV26.16, U4.71 ((AD7)PA7)
LCD_DI: SV26.6, U4.64 (PJ1(TXD3/PCINT10))
LCD_EN: SV26.8, U4.63 (PJ0(RXD3/PCINT9))
MISO: R29.2, SV15.1, T4.3 (C), U4.22 ((MISO/PCINT3)PB3)
MOSI: R22.2, SV15.4, U4.21 ((MOSI/PCINT2)PB2)
M_RX0: SV27.3, U4.2 ((RXD0/PCIN8)PE0)
M_RX1: SV28.3, U4.45 ((RXD1/INT2)PD2)
M_RX2: SV29.3, U4.12 (PH0(RXD2))
M_TX0: R21.1, U4.3 ((TXD0)PE1)
M_TX1: R20.1, U4.46 ((TXD1/INT3)PD3)
M_TX2: R19.1, U4.13 (PH1(TXD2))
unnamed: C12.1, R14.1, R16.2
unnamed: C10.1, R12.1, SV26.17
unnamed: R18.2, T2.3 (C)
unnamed: R16.1, T2.2 (B)
unnamed: C11.1, R13.1, R17.2
unnamed: R21.2, SV27.2
unnamed: R20.2, SV28.2
unnamed: R19.2, SV29.2
unnamed: C1.2, Q1.2, U4.33 (XTAL2)
unnamed: C2.2, Q1.1, U4.34 (XTAL1)
unnamed: T4.1 (E), U$1.7 (DAT0_DO)
unnamed: OK1.4 (COL), SV1.3
unnamed: R11.1 (CCW), SV26.18
unnamed: R11.2 (WIPER), SV26.5
unnamed: R18.1, SV26.20
unnamed: R24.2, R27.1, U$1.2 (CD_DAT3_CS)
unnamed: R22.1, R26.1, U$1.3 (CMD_DIN)
unnamed: R23.2, R25.1, U$1.5 (CLK)
unnamed: R28.1, T4.2 (B)
unnamed: R17.1, T3.2 (B)
unnamed: D2.A, SV30.2, T3.3 (C)
unnamed: D2.C, R15.2, SV30.1
unnamed: R6.1, T1.2 (B)
unnamed: D1.C, R6.2, SV16.2
unnamed: OK1.3 (EMIT), R1.1
unnamed: C4.2, Q2.2 (S), R4.2, R7.2, SV1.4, SV1.5, SV17.3
unnamed: C4.1, Q2.1 (G), R7.1, SV17.1, T1.3 (C)
unnamed: OK1.2 (C), R3.2
unnamed: R4.1, SV16.3
unnamed: C5.+, D3.C, Q2.3 (D), SV17.2, U2.3 (IN), U3.3 (IN)
POW_LATCH: D1.A, U4.26 ((OC0A/OC1C/PCINT7)PB7)
POW_OFF: R5.1, SV16.1, U4.25 ((OC1B/PCINT6)PB6)
RESET: R8.1, SV15.5, SV27.1, U4.30 (RESET)
SCK: R23.1, SV15.3, U4.20 ((SCK/PCINT1)PB1)
SCL: R9.2, U1.6 (SCL), U4.43 ((SCL/INT0)PD0)
SDA: R10.2, U1.5 (SDA), U4.44 ((SDA/INT1)PD1)
SPKR: R13.2, U4.7 ((OC3C/INT5)PE5)
SS: R24.1, U4.19 ((SS/PCINT0)PB0)
SWA_DN: SV2.1, U4.54 ((A9)PC1)
SWA_UP: SV2.3, U4.53 ((A8)PC0)
SWB_DN: SV3.1, U4.56 ((A11)PC3)
SWB_UP: SV3.3, U4.55 ((A10)PC2)
SWC_DN: SV4.1, U4.58 ((A13)PC5)
SWC_UP: SV4.3, U4.57 ((A12)PC4)
SWD_DN: SV5.1, U4.60 ((A15)PC7)
SWD_UP: SV5.3, U4.59 ((A14)PC6)
SWE_DN: SV6.1, U4.24 ((OC1A/PCINT5)PB5)
SWE_UP: SV6.3, U4.23 ((OC2A/PCINT4)PB4)
SWF_DN: SV7.1, U4.52 ((RD)PG1)
SWF_UP: SV7.3, U4.51 ((WR)PG0)
SWG_DN: SV8.1, U4.82 (PK7(ADC15/PCINT23))
SWG_UP: SV8.3, U4.90 ((ADC7/TDI)PF7)
SWH_DN: SV9.1, U4.50 ((T0)PD7)
SWH_UP: SV9.3, U4.5 ((OC3A/AIN1)PE3)
TRIM_X1_DN: SV13.1, U4.35 (PL0(ICP4))
TRIM_X1_UP: SV13.3, U4.36 (PL1(ICP5))
TRIM_X2_DN: SV10.1, U4.41 (PL6)
TRIM_X2_UP: SV10.3, U4.42 (PL7)
TRIM_Y1_DN: SV12.1, U4.37 (PL2(T5))
TRIM_Y1_UP: SV12.3, U4.38 (PL3(OC5A))
TRIM_Y2_DN: SV11.1, U4.39 (PL4(OC5B))
TRIM_Y2_UP: SV11.3, U4.40 (PL5(OC5C))
X1_AXIS: C16.2, SV23.2, U4.94 ((ADC3)PF3)
X2_AXIS: C13.2, SV20.2, U4.97 ((ADC0)PF0)
X3_AXIS: C20.2, SV31.2, U4.86 (PK3(ADC11/PCINT19))
X4_AXIS: C22.2, SV33.2, U4.84 (PK5(ADC13/PCINT21))
Y1_AXIS: C15.2, SV22.2, U4.95 ((ADC2)PF2)
Y2_AXIS: C14.2, SV21.2, U4.96 ((ADC1)PF1)
Y3_AXIS: C21.2, SV32.2, U4.87 (PK2(ADC10/PCINT18))
Y4_AXIS: C23.2, SV34.2, U4.85 (PK4(ADC12/PCINT20))
Z1_AXIS: C8.1, SV19.2, U4.88 (PK1(ADC9/PCINT17))
Z2_AXIS: C9.2, SV18.2, U4.89 (PK0(ADC8/PCINT16))

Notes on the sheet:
Spkr 8ohm 0.25W
!CS1 !CS2 GND VCC V0 RS R/W E D0 D1 D2 D3 D4 D5 D6 D7 !RST VEE A K
GND
VBATT
Power connector
The max voltage here should not exceed 4.9V, so the resistors in this voltage divider should be sized appropriately
Power switch (Slide type)
V_IN
V_IN is 7-9V. VBATT and V_IN can be shorted together e.g. when using 2 series Li-ion cells.
SWA
SWB
SWC
SWD
SWE
SWF
SWG
SWH
LCD
UART0
UART1
BUTTONS
TRIMS
ROLL
PITCH
THR
YAW
KNOB_A
KNOB_B
NOTES: - MCU pins marked with x have no arduino mapping. They can be used but they have no connector headers on arduino boards, hence have been avoided here. - For two position switches, the UP signal is left unconnected. - The Z axes are optional. - Uart0 is used for firmware uploads - Uart1 for r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
Place holder for TO-220 package
UART2
MICRO SD CARD

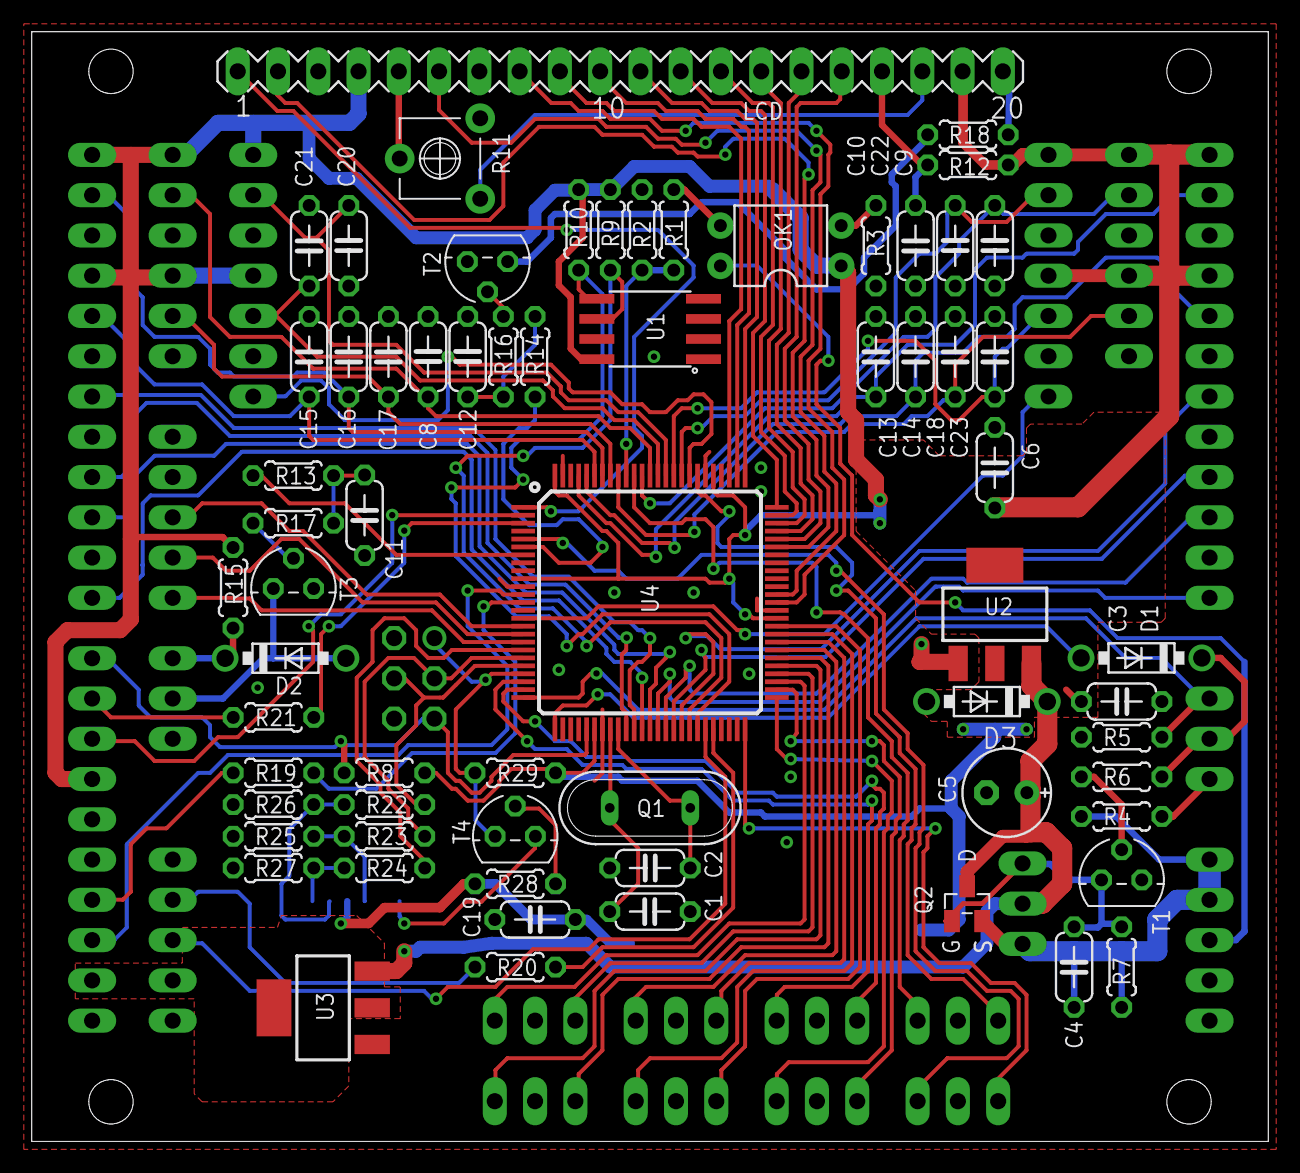
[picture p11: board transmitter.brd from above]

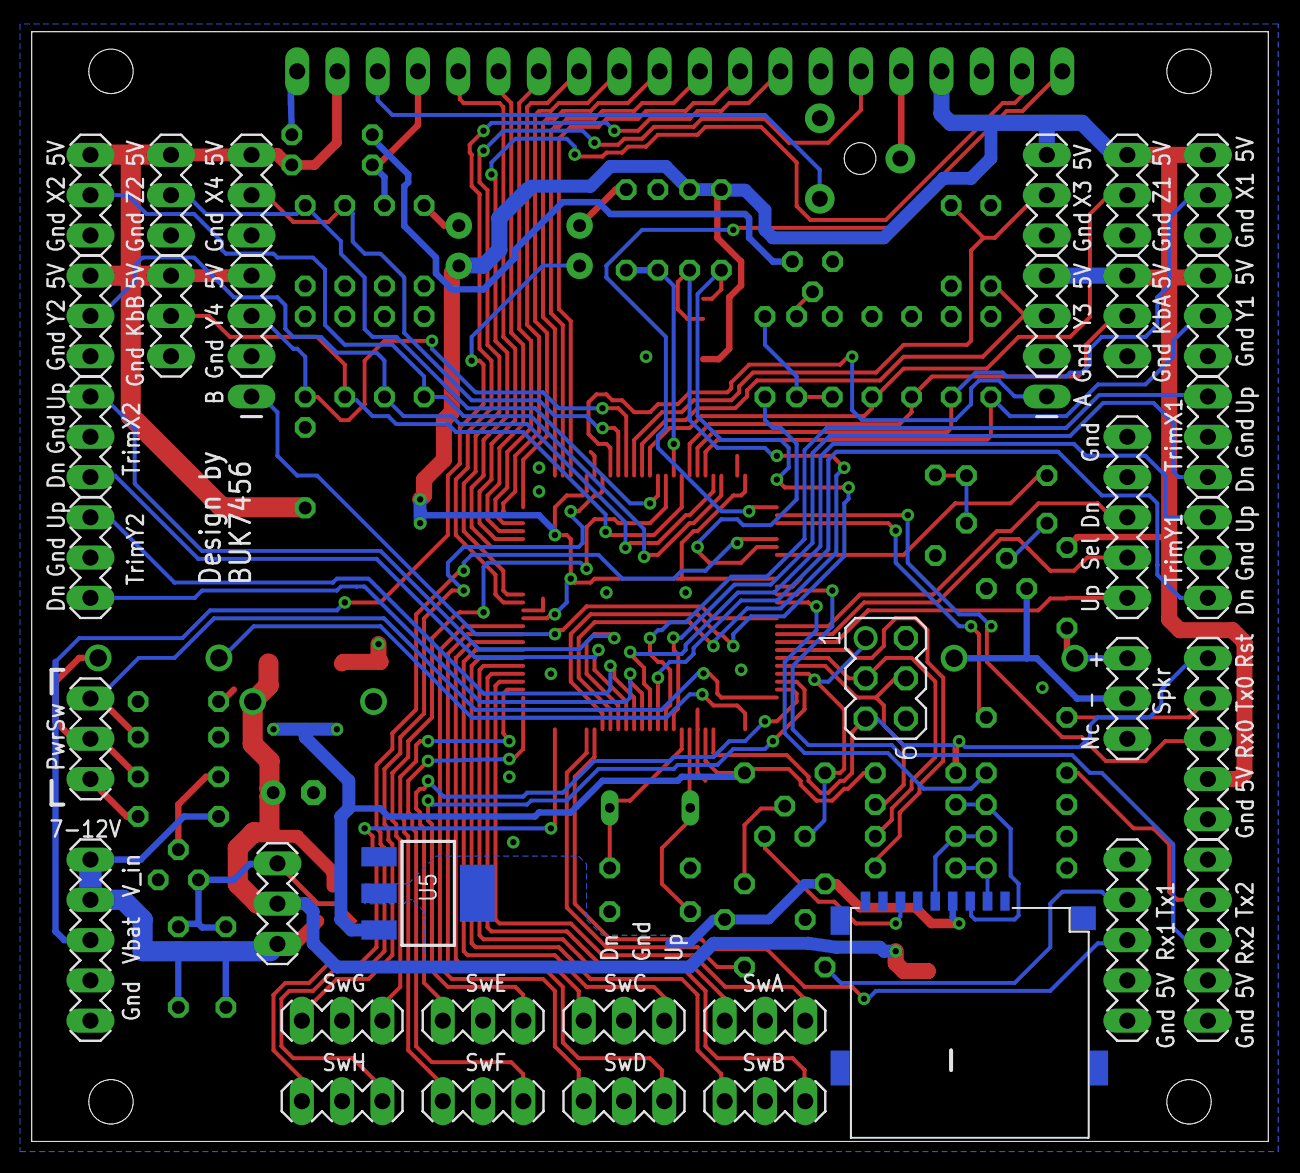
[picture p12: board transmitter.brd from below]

Board: 2 copper layers, 78.0 x 70.0 mm, 103 parts (37 on the bottom side), 105 nets.

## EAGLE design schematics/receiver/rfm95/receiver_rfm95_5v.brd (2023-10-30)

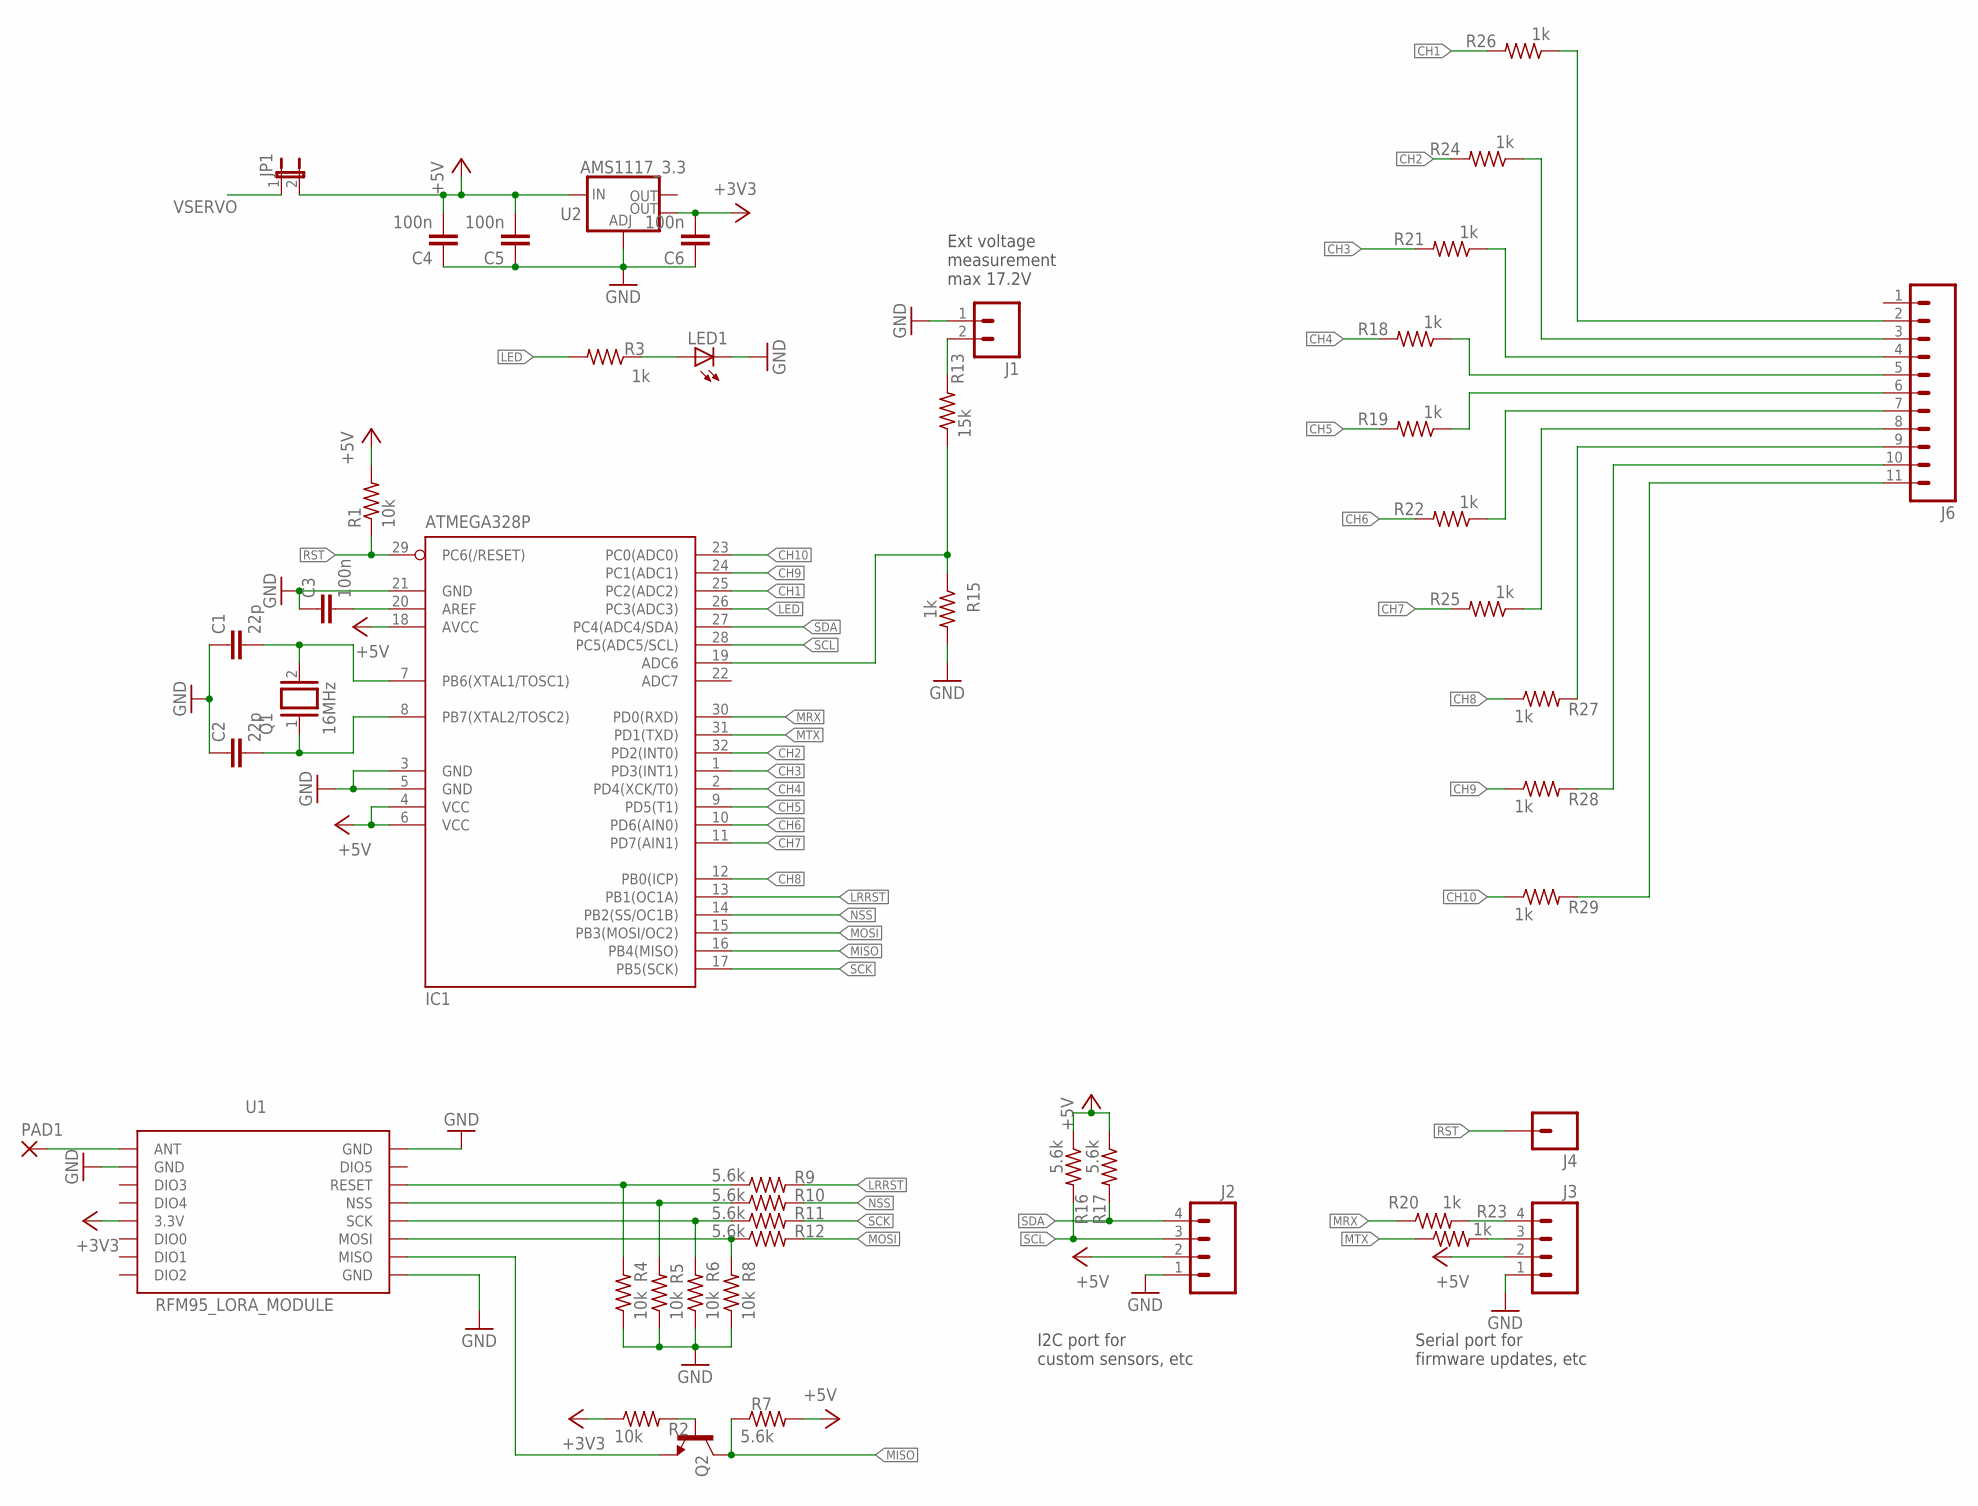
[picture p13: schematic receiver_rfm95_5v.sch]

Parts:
C1, C2: 22p; C0805K
C3, C4, C5, C6: 100n; C0805K
IC1: ATMEGA328P; TQFP32-08
J1: M02PTH; 1X02
J2, J3: M04PTH; 1X04
J4: M01PTH; 1X01
J6: M11PTH; 1X11
JP1: JP1E; JP1
LED1: LEDCHIPLED_1206; CHIPLED_1206
PAD1: 2,15/1,0
Q1: 16MHz; QS
Q2: BC817-16SMD; SOT23-BEC
R1, R2, R4, R5, R6, R8: 10k; R0805
R3, R15, R18, R19, R20, R21, R22, R23, R24, R25, R26, R27, R28, R29: 1k; R0805
R7, R9, R10, R11, R12, R16, R17: 5.6k; R0805
R13: 15k; R0805
U1: RFM95_LORA_MODULE; RFM95
U2: AMS1117_3.3; SOT223

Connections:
+3V3: C6.2, R2.1, U1.3.3V, U2.4 (OUT)
+5V: C4.2, C5.2, IC1.4 (VCC), IC1.6 (VCC), IC1.18 (AVCC), J2.2, J3.2, JP1.2, R1.2, R7.2, R16.1, R17.1, U2.3 (IN)
CH1: IC1.25 (PC2(ADC2)), R26.2
CH2: IC1.32 (PD2(INT0)), R24.2
CH3: IC1.1 (PD3(INT1)), R21.2
CH4: IC1.2 (PD4(XCK/T0)), R18.2
CH5: IC1.9 (PD5(T1)), R19.2
CH6: IC1.10 (PD6(AIN0)), R22.2
CH7: IC1.11 (PD7(AIN1)), R25.2
CH8: IC1.12 (PB0(ICP)), R27.1
CH9: IC1.24 (PC1(ADC1)), R28.1
CH10: IC1.23 (PC0(ADC0)), R29.1
DIO3: U1.DIO3
GND: C1.1, C2.1, C3.1, C4.1, C5.1, C6.1, IC1.3 (GND), IC1.5 (GND), IC1.21 (GND), J1.1, J2.1, J3.1, LED1.C, R4.1, R5.1, R6.1, R8.1, R15.2, U1.GND, U1.GND@1 (GND), U1.GND@2 (GND), U2.1 (ADJ)
LED: IC1.26 (PC3(ADC3)), R3.2
LRRST: IC1.13 (PB1(OC1A)), R9.2
MISO: IC1.16 (PB4(MISO)), Q2.C, R7.1
MOSI: IC1.15 (PB3(MOSI/OC2)), R12.2
MRX: IC1.30 (PD0(RXD)), R20.1
MTX: IC1.31 (PD1(TXD)), R23.1
unnamed: C1.2, IC1.7 (PB6(XTAL1/TOSC1)), Q1.2
unnamed: J6.10, R28.2
unnamed: C2.2, IC1.8 (PB7(XTAL2/TOSC2)), Q1.1
unnamed: J6.9, R27.2
unnamed: R4.2, R9.1, U1.RESET
unnamed: R5.2, R10.1, U1.NSS
unnamed: R6.2, R11.1, U1.SCK
unnamed: R8.2, R12.1, U1.MOSI
unnamed: Q2.E, U1.MISO
unnamed: C3.2, IC1.20 (AREF)
unnamed: IC1.19 (ADC6), R13.1, R15.1
unnamed: J3.3, R23.2
unnamed: LED1.A, R3.1
unnamed: PAD1.1, U1.ANT
unnamed: J6.2, R26.1
unnamed: J3.4, R20.2
unnamed: J6.3, R24.1
unnamed: J6.4, R21.1
unnamed: J6.5, R18.1
unnamed: J6.6, R19.1
unnamed: J6.7, R22.1
unnamed: J6.8, R25.1
unnamed: Q2.B, R2.2
unnamed: J1.2, R13.2
unnamed: J6.11, R29.2
NSS: IC1.14 (PB2(SS/OC1B)), R10.2
RST: IC1.29 (PC6(/RESET)), J4.1, R1.1
SCK: IC1.17 (PB5(SCK)), R11.2
SCL: IC1.28 (PC5(ADC5/SCL)), J2.3, R16.2
SDA: IC1.27 (PC4(ADC4/SDA)), J2.4, R17.2
VSERVO: JP1.1

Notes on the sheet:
I2C port for custom sensors, etc
Serial port for firmware updates, etc
Ext voltage measurement max 17.2V

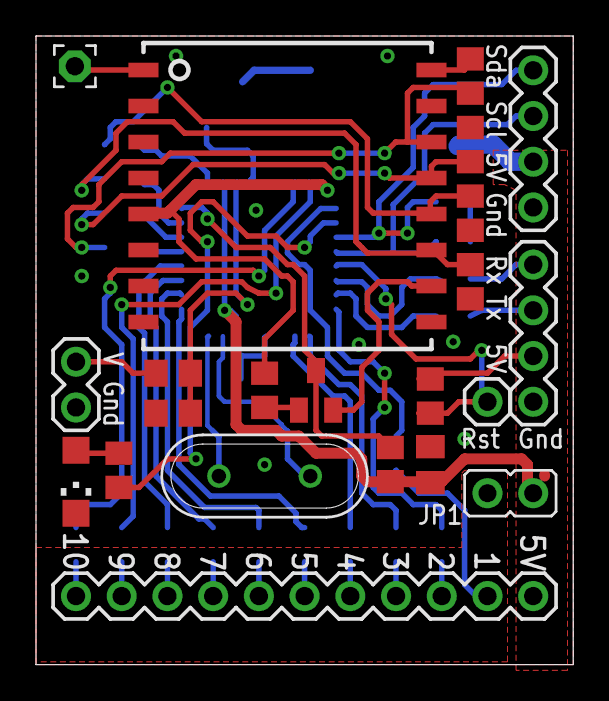
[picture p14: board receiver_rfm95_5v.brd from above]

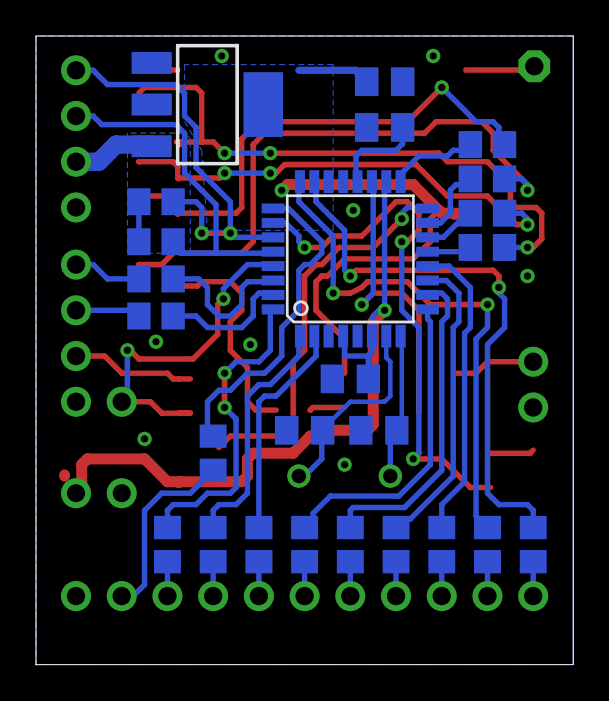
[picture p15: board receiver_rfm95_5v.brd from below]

Board: 2 copper layers, 29.8 x 34.9 mm, 47 parts (25 on the bottom side), 49 nets.

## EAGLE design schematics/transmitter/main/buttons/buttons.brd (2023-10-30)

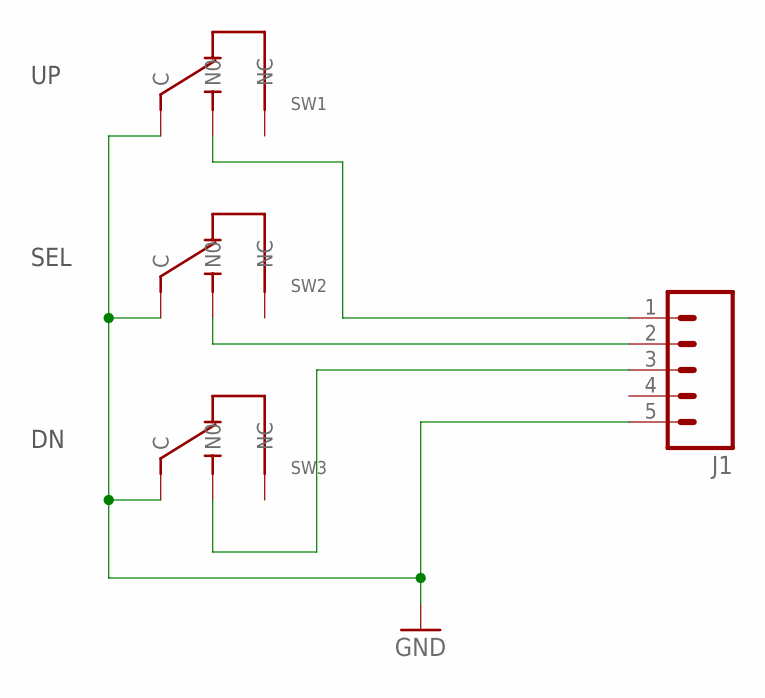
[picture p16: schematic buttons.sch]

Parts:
J1: M05PTH; 1X05
SW1, SW2, SW3: MICROSWITCH

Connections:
GND: J1.5, SW1.C, SW2.C, SW3.C
unnamed: J1.1, SW1.NO (N0)
unnamed: J1.3, SW3.NO (N0)
unnamed: J1.2, SW2.NO (N0)

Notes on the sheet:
SEL

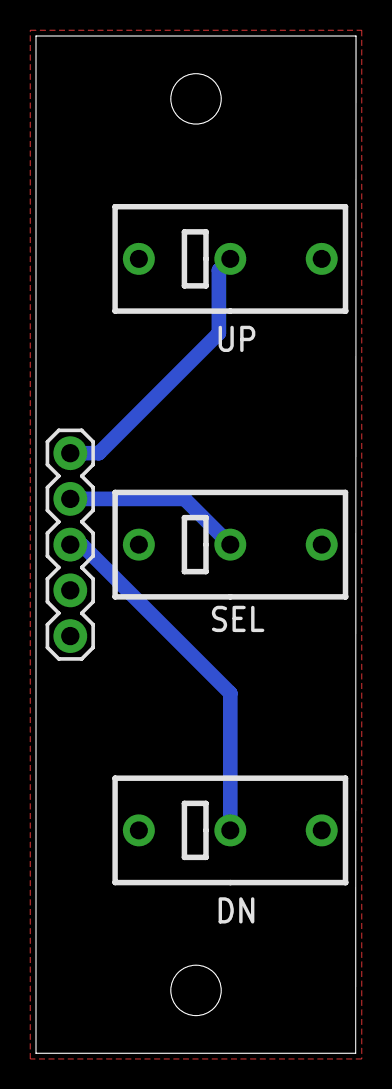
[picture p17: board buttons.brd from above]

Board: 2 copper layers, 17.8 x 56.5 mm, 4 parts (0 on the bottom side), 4 nets.

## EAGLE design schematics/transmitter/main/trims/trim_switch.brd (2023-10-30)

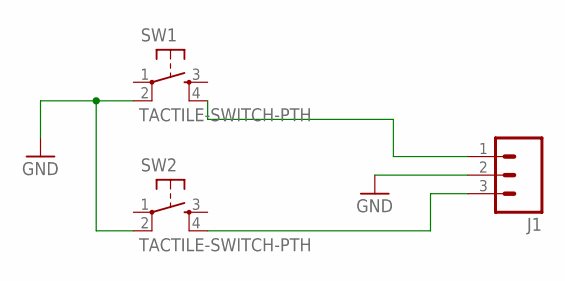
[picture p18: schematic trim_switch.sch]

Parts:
J1: M03PTH; 1X03
SW1, SW2: TACTILE-SWITCH-PTH; TAC-SWITCH-PTH

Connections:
GND: J1.2, SW1.2, SW2.2
unnamed: J1.1, SW1.4
unnamed: J1.3, SW2.4

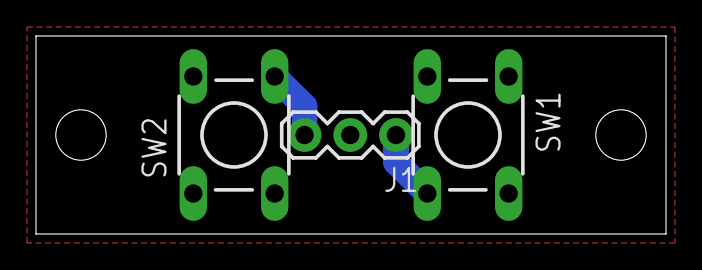
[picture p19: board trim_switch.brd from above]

Board: 2 copper layers, 35.0 x 11.0 mm, 3 parts (0 on the bottom side), 3 nets.

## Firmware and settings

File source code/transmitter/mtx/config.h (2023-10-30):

/*
 * config.h
 *
 * Basic settings such as:
 * - LCD controller
 * - UI to use
 * - Pin mapping
 * - External EEPROM 
 *
 */

#ifndef _CONFIG_H_
#define _CONFIG_H_

#define _SKETCHVERSION "1.0"

//===========================================================================
//============================= LCD and UI ==================================
//===========================================================================

#define UI_128X64
// #define UI_84X48  //not implemented

#define DISPLAY_KS0108  
// #define DISPLAY_PCD8544 //not implemented

//===========================================================================
//============================= Pins and ports ==============================
//===========================================================================

//Name                 Arduino Pin

#define PIN_X1_AXIS      A3
#define PIN_Y1_AXIS      A2
#define PIN_X2_AXIS      A0
#define PIN_Y2_AXIS      A1
#define PIN_X3_AXIS      A11
#define PIN_Y3_AXIS      A10
#define PIN_X4_AXIS      A13
#define PIN_Y4_AXIS      A12

#define PIN_KNOB_A       A4
#define PIN_KNOB_B       A5

#define PIN_BATTVOLTS    A6

#define PIN_LCD_BACKLIGHT   2
#define PIN_BUZZER          3

#define PIN_POWER_OFF_SENSE 12
#define PIN_POWER_LATCH     13

#define PIN_KEY_SELECT   8
#define PIN_KEY_UP       9
#define PIN_KEY_DOWN     7

#define PIN_KS_EN        15
#define PIN_KS_RS        14
#define PIN_KS_CS1       4
#define PIN_KS_CS2       39

//--- Direct port manipulation

#define DDRx_LCD_DATA    DDRA
#define PORTx_LCD_DATA   PORTA

#define DDRx_TRIMS   DDRL
#define PORTx_TRIMS  PORTL
#define PINx_TRIMS   PINL

//--- Physical switches

//Name             Arduino Pin
#define PIN_SWA_UP   37
#define PIN_SWA_DN   36

#define PIN_SWB_UP   35
#define PIN_SWB_DN   34

#define PIN_SWC_UP   33
#define PIN_SWC_DN   32

#define PIN_SWD_UP   31
#define PIN_SWD_DN   30

#define PIN_SWE_UP   10
#define PIN_SWE_DN   11

#define PIN_SWF_UP   41
#define PIN_SWF_DN   40

#define PIN_SWG_UP   61
#define PIN_SWG_DN   69

#define PIN_SWH_UP   5
#define PIN_SWH_DN   38

//--- sd card

#define PIN_SD_CS    53

//===========================================================================
//============================= External EEPROM =============================
//===========================================================================

//--- 24LC256
//Total bytes (256*1024)/8 => 32768
#define EXTERNAL_EEPROM_TOTAL_BYTES     32768
#define EXTERNAL_EEPROM_PAGE_BYTES      32
#define EXTERNAL_EEPROM_DEVICE_ADDRESS  0x0

/* 
//--- 24LC32
//Total bytes (32*1024)/8 => 4096
#define EXTERNAL_EEPROM_TOTAL_BYTES     4096
#define EXTERNAL_EEPROM_PAGE_BYTES      32
#define EXTERNAL_EEPROM_DEVICE_ADDRESS  0x7
 */

#endif

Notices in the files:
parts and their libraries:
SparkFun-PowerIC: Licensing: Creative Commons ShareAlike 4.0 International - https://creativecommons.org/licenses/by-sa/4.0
